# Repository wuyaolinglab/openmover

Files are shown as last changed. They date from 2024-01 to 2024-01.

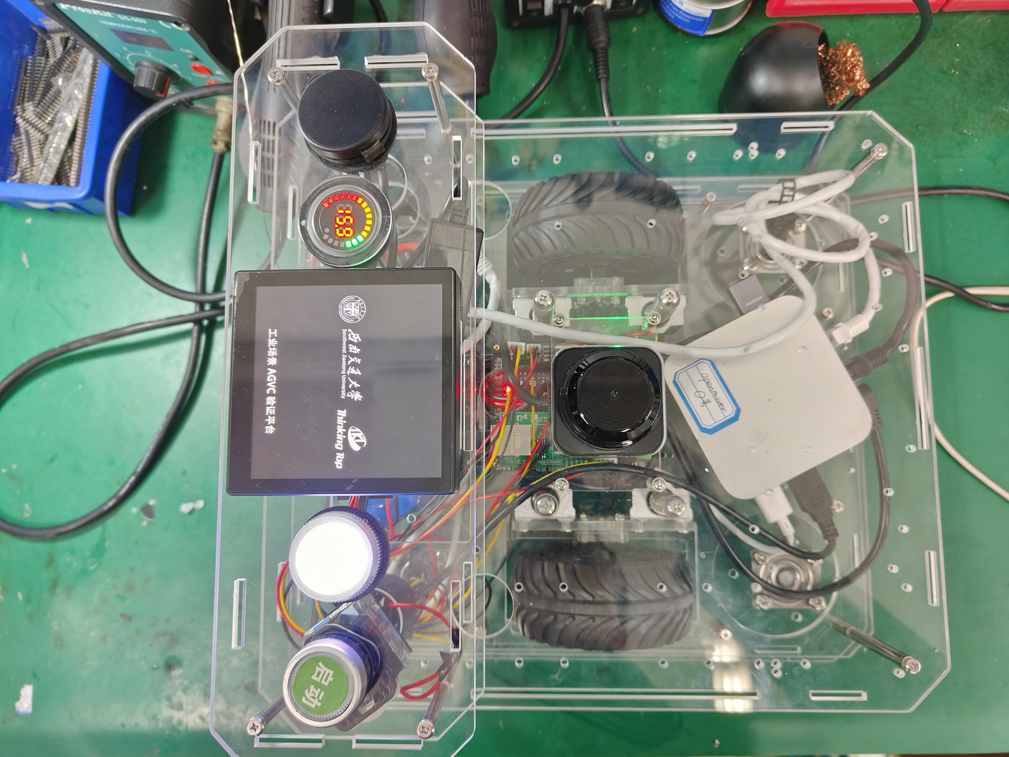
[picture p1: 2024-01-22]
相关图片/1.0原型机/顶部.jpg

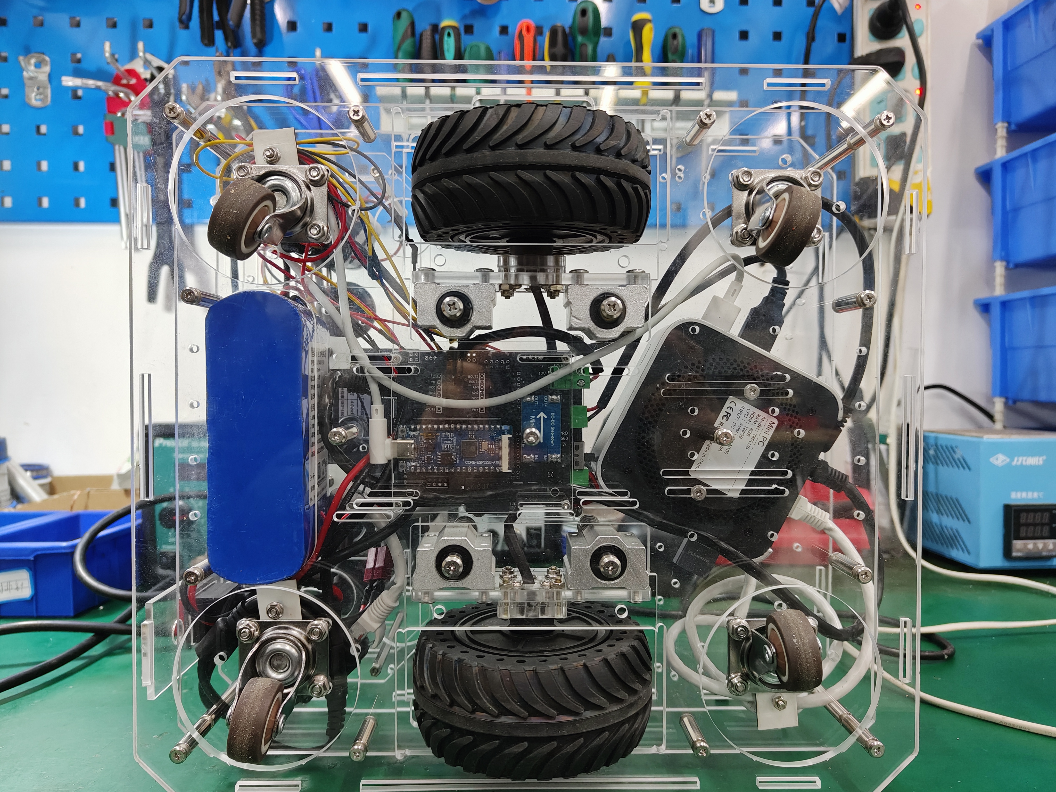
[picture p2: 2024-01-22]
相关图片/1.0原型机/底部.jpg

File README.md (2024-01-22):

# OPENMOVER

> 基于ROS的开源AGV机器人底盘

## 项目初衷

一切的源头来源于一个疑问：**有没有能陪伴我们从入门学习ROS到场景实际使用的机器人底盘开发项目？**

当我们打开淘宝浏览机器人底盘时，可以看到诸多基于树莓派和Jetson的小型ROS机器人底盘，也不乏体积庞大的工业级搬运底盘，前者往往只能陪伴我们度过最开始的学习开发，往往其结构与硬件绑定公司其他相关产品，因而我们在学习时的知识体系并不完善，需要我们之后单独学习底盘的结构设计以及电气控制部分；后者则往往不开放让我们进行学习开发的接口，结构上较为复杂且难以拆卸，往往其主控中的系统也并非基于ROS框架……

后来，带着上面的疑问我们开始围绕机器人底盘进行探索性的开发，我们一直在探索着如何保证低成本地简化工业底盘结构，如无必要勿增实体的思想指导着我们避免市面上的ROS机器人底盘为追求低成本和高销量而做出的无用设计，让结构尽可能简单；电气控制上尽可能简化到以模块为主，借鉴市面上的控制底盘没有冗余设计的教训，同时给容易坏、难设计的电源芯片、电机控制等部分预留更换可能，可能避免初学者因底盘的设计以及器件的偶尔损耗维修消磨兴趣……

再后来，我们在结合前面的诸多教训的基础上推出了OPENMOVER这个项目，希望能以这个项目来总结我们在前面探索机器人底盘设计中的经验与教训，将完整的机器人底盘设计思路提供给有意向探索机器人设计与应用的初学者，我们并非希望他们能避开机器人开发学习中的问题，只是更希望他们能在之后的开发设计中遇到问题时能对三个维度展开思考：我们的机器人要完成什么任务？为完成任务需要具备什么能力？为实现该能力，我的结构、硬件、软件设计有几种思路？

机器人的设计本质也是基于人的需要，设计一套复杂的系统并非我们的项目初衷，我们不愿意看到初学者迷失于技术之中，为自己贴上结构、硬件、软件开发的标签，而是去思考当我们作为用户去使用这套机器人时，我们希望得到什么？

当然啦，作为初版的设计者，我们希望这套机器人底盘足够简单可靠，能装上机械臂、举升平台、工程巡检设备等，能在不对结构进行较大改变的情况下拓展足够多的应用场景，从教学中应用到我们的实际业务场景中去，当然，我们的探索还在继续……

本项目遵循[Apache-2.0 license](https://github.com/wuyaolinglab/openmover#)协议

## 整体结构设计

更新时间24.1.22，版本1.0

### 1.0版本

设计导图文件可点击[这里查看](https://github.com/wuyaolinglab/openmover/tree/main/相关图片/1.0版结构与主控设计导图.png)

原型车图片可点击[这里查看](https://github.com/wuyaolinglab/openmover/tree/main/相关图片/1.0原型机)

1.0初版整车尺寸300x320xmm，整体结构采用双差速轮+四从动万向轮的结构，差速轮选用微雪DDSM115直驱伺服轮毂电机，四万向轮理论合计承重最高50KG

初版在外观结构上主要参考了海康威视AGV中的Q2系列LMR潜伏式机器人，并针对原有结构提出如下简化改进以及设计需要：

1. 主轮悬挂：主动轮添加悬挂结构，以保证整车在平地的路面适应能力以及运动性能
2. 雷达视野：初版使用蓝海LDS-50C-C30E单线TOF激光雷达，增大单线雷达的可视范围，减少结构上的遮挡角度范围
3. 较小尺寸：减小整车的尺寸，尽可能控制在320*320mm以内
4. 分层设计：保证整车的拓展能力，采用分层结构设计，底盘与可拓展部分为松耦合关系
5. 底盘布局：预留底盘内部拓展空间，方便理线与拓展元件
6. 电池限位：因供电需要至少4S电池组供电，尽可能在结构中加入单独的电池仓以防止电池固定不稳引发的安全问题
7. 负载能力：为保证整车的负载能力，底盘整体应尽可能考虑到受力均匀给到四个万向轮

我们提供了多种雷达的安装孔位，我们原型车使用到的是蓝海LDS-50C-C30E雷达，使用网口与工控机进行通讯，考虑到这款雷达可能不易在市场上购得，我们也测试过使用比较易得的镭神N10P系列雷达，大家可以根据手头的雷达安装孔位进行修改

## 底盘主控设计

更新时间24.1.20，版本1.1

### 1.1版本

初版底盘控制板采用合宙ESP32S3作为主控，工控机通过网口连接板载的有人双路UART转以太网模块USR-TCP232-E连接底盘主控以及串口屏，后续将上传以树莓派PICO作为主控，通过UART串口转USB模块与工控机进行通讯的方案

该版本的主要的考虑到的设计要点如下：

1. 尽可能减少贴片与插件元件的焊接，尽可能使用现有模块
2. 使用485总线转UART模块控制微雪伺服轮毂电机
3. 能控制双路有刷电池
4. 拥有外置灯效与按钮控制接口
5. 双路12V电源输出，支持的最大电流应保证在3A以上
6. 使用双路UART转以太网模块与工控机进行通讯，主控Type-C接口主要用于供电，后期将脱离使用
7. 底盘主控使用FreeRTOS系统，但为方便初学者烧录使用Arduino或PlatformIO作为开发平台

## 控制系统框架

更新时间24.1.20

底盘使用搭建了Ubuntu20.04.6操作系统的ROS [Noetic](http://wiki.ros.org/noetic/Installation/Ubuntu)作为机器人系统框架

相关例程适配代码将在后续更新中提供

## 物料清单及配件说明

本车物料均可于淘宝平台上购买、加工

主要元件为：

| 元件 | 型号 | 参考价格 |
| --- | --- | --- |
| TOF激光雷达 | [蓝海LDS-50C-C30E](https://detail.tmall.com/item.htm?id=670105361941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) | 2000 |
| TOF激光雷达 | [镭神N10P](https://item.taobao.com/item.htm?id=661905067052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) | 571.2 |
| 轮毂电机 | [微雪DDSM115直驱伺服电机](https://detail.tmall.com/item.htm?id=693013835916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) | 392 |
| N100工控机 | [T8PLUS/N100/DDR5](https://item.taobao.com/item.htm?id=690024926005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) | 740 |
| 14.8V锂电池组 | [亿森能14.8V10500毫安](https://item.taobao.com/item.htm?_u=l209b8sqkle3cb&id=723067674262&spm=a1z09.2.0.0.533a2e8dcV89pz) | 160 |
| 金属板材切割  | [5052铝板加工](https://item.taobao.com/item.htm?_u=l209b8sqkl377d&id=638490665708&spm=a1z09.2.0.0.418e2e8dOwLTBY) | 230~260  |

详细的物料清单将于下一更新中提供

## 上传说明

最近一次上传更新时间为24.1.20，整体版本1.0

项目文件与代码正在陆续上传更新中

***24.1.20*** 第一次上传，主要包括整车的结构设计、初版底盘控制板文件和简单物料清单

***24.1.22*** 第二次上传，修正了第一次上传中整车的结构设计细节，更新了说明资料包括图片、加工文件、模块说明文件，上传了相关配件的初版物料清单

## 更新计划

下一上传时间预计在24.1.25日前，预期更新版本为1.0

1. 增加整车的结构扩展说明，包括机械臂及举升平台的拓展设计安装方案
2. 更新整车的结构设计细节说明，同时准备上传ROS相关控制程序及初版说明
3. 增加对整体设计的说明
4. 更新参考资料及相关说明

## 收集意见

希望大家能在issues中提出你们对小车的改进与应用意见，我们将会及时回复并在整理后以月报进行发布

## 关于我们

本项目来自西南交通大学工训中心A510实验室团队

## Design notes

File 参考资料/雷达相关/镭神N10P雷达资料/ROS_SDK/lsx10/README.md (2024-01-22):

# lslidar

## Description

The `lslidar` package is a linux ROS driver for lslidar M10 ,L10,M10_GPS,M10_P,M10_PLUS and N10.
The package is tested on Ubuntu 20.04 with ROS indigo.

## Compling

This is a Catkin package. Make sure the package is on `ROS_PACKAGE_PATH` after cloning the package to your workspace. And the normal procedure for compling a catkin package will work.

```
cd your_work_space
catkin_make 
source devel/setup.bash
roslaunch lslidar_driver lslidar_net.launch 				(网口版雷达)
roslaunch lslidar_driver lslidar_serial.launch 				(串口版雷达)
```

open new terminal
rostopic pub -1 /lslidar_order std_msgs/Int8 "data: 1"		(open radar)
rostopic pub -1 /lslidar_order std_msgs/Int8 "data: 0"		(close radar)

```
open new terminal
source devel/setup.bash 
rostopic echo /difop_information					(printf information)
## Example Usage

### lslidar_m10_driver

**Parameters**

`device_ip` (`string`, `default: 192.168.1.222`)

By default, the IP address of the device is 192.168.1.222.

`frame_id` (`string`, `default: lslidar`)

The frame ID entry for the sent messages.

**Published Topics**

`lslidar_packets` (`lslidar_m10_msgs/LslidarM10Packet`)

Each message corresponds to a lslidar packet sent by the device through the Ethernet.

### lslidar_m10_decoder

**Parameters**

`min_range` (`double`, `0.3`)

`max_range` (`double`, `100.0`)

Points outside this range will be removed.

`frequency` (`frequency`, `20.0`)

Note that the driver does not change the frequency of the sensor. 

`publish_point_cloud` (`bool`, `false`)

If set to true, the decoder will additionally send out a local point cloud consisting of the points in each revolution.

**Published Topics**

`lslidar_sweep` (`lslidar_m10_msgs/LslidarM10Sweep`)

The message arranges the points within each sweep based on its scan index and azimuth.

`lslidar_point_cloud` (`sensor_msgs/PointCloud2`)

This is only published when the `publish_point_cloud` is set to `true` in the launch file.

**Node**

```

roslaunch lslidar_driver lslidar_net.launch

```

Note that this launch file launches both the driver and the decoder, which is the only launch file needed to be used.

## FAQ

## Bug Report

Prefer to open an issue. You can also send an E-mail to shaohuashu@lslidar.com

RERTION 
V0.1 2000 points per circle
v0.2 1000 points per circle

```

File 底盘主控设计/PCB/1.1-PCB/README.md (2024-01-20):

How to use：

At editor, open the document via: Top menu - File - Open - EasyEDA... , and select the json file, then open it at the editor, you can save it into a project.

如何使用：

打开编辑器，通过：顶部菜单 - 文件 - 打开 - 立创EDA... ，选择 json 文件打开在编辑器，你可以保存文档进工程里面。

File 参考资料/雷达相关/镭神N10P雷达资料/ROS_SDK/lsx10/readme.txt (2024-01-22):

版本变更
/***************************************************************
初始版本: LSLIDAR_M10_N10_V2.5.0_221103_ROS
变更内容: 
	1.实现M10/M10_P/M10_PLUS/N10/M10_GPS网口和串口传输数据生成点云功能
    	2.实现点云角度裁剪和距离过滤功能
    	3.可以通过lslidar_order话题控制雷达启
    	4.支持读取pcap包
	
更改日期: 2022-11-03
***************************************************************/

/***************************************************************
初始版本: LSLIDAR_M10_N10_V2.5.0_221103_ROS
变更版本: LSLIDAR_M10_N10_V2.5.1_221130_ROS
变更内容: 
	1.新增L10雷达。
	2.针对M10_P雷达出现的点云问题进行紧急修复。
	3.针对M10和M10_GPS雷达在最近出货雷达出现的点云问题进行紧急修复。
	4.修复循环索取新内存导致机器卡死bug。
	5.更新M10_P和M10_PLUS雷达协议。
	6.修复角度值分配错误问题。
	
更改日期: 2022-11-30
***************************************************************/
/***************************************************************
初始版本: LSLIDAR_M10_N10_V2.5.1_221130_ROS
变更版本: LSLIDAR_M10_N10_V2.5.2_230110_ROS
变更内容: 
	1.日常检测到驱动的包头检测有bug
	2.更新M10系列的角度补偿方法。
	3.修复发现的点角度不连续bug。
	4.添加可选择是否发布pointcloud2话题。
	5.添加可选择是否发布scan话题。
	6.添加双回波解析方法
	7.添加N10_P雷达选择1
	8.添加读txt文件功能
更改日期: 2023-01-10
***************************************************************/

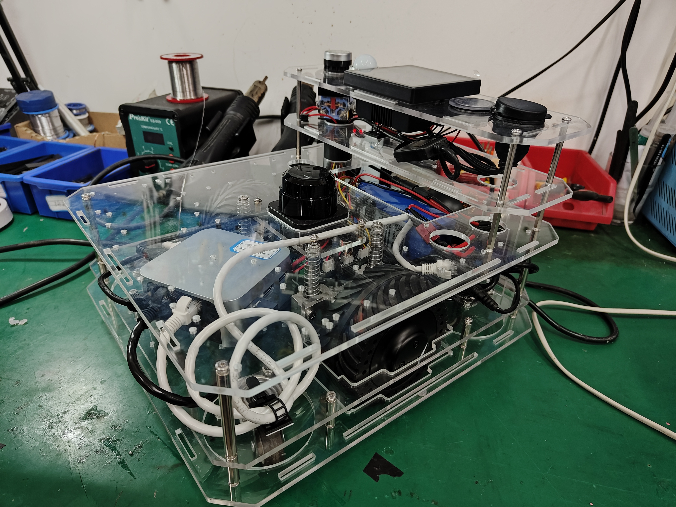
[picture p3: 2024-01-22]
相关图片/1.0原型机/前视图.jpg

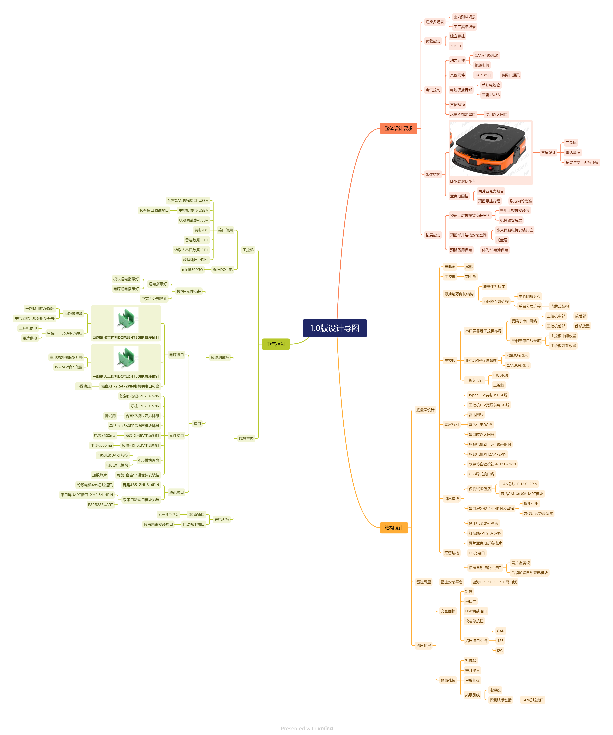
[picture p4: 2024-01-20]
相关图片/1.0版结构与主控设计导图.png

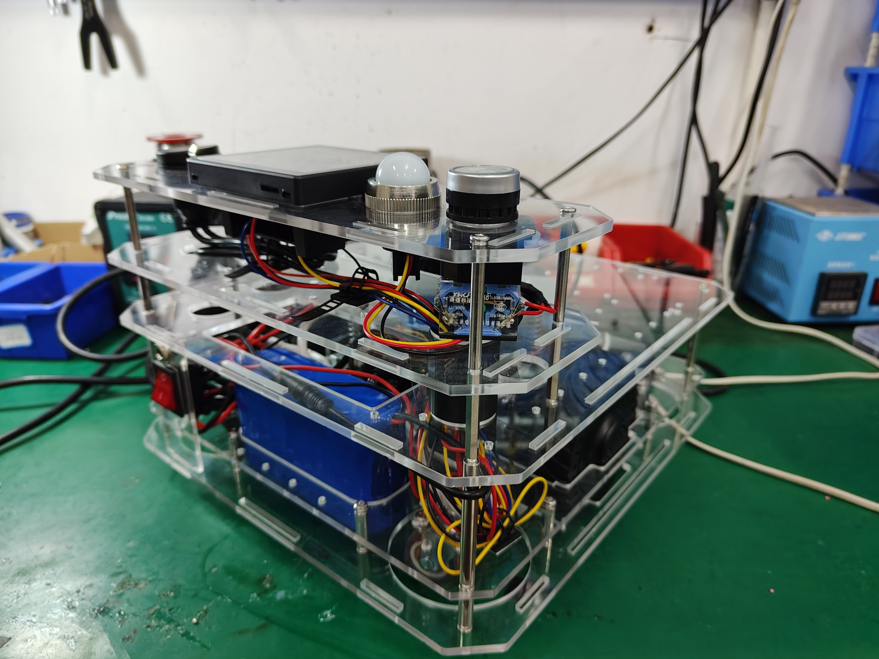
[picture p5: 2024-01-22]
相关图片/1.0原型机/后视图.jpg

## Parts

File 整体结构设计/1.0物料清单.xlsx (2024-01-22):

序号 | 所属模块 | 名称 | 规格型号 | 数量 | 单位 | 参考链接 | 备注
1 | 雷达 | 蓝海40m单线激光网口雷达 | LDS-50C-C30E | 1 | 个 | https://detail.tmall.com/item.htm?abbucket=15&id=670105361941&ns=1&skuId=4998133087692
2 | 雷达 | 镭神25m激光串口雷达 | N10P | 1 | 个 | https://item.taobao.com/item.htm?abbucket=17&id=661905067052&ns=1&skuId=5100312911950
3 | 电机 | 微雪直驱伺服电机 | DDSM115 | 2 | 台 | https://item.taobao.com/item.htm?_u=m209b8sqklf7e5&id=692477501151&skuId=5184823387964
4 | 工控机 | N100 mini主机电脑 | T8PLUS-8G内存-128GB存储 | 1 | 台 | https://item.taobao.com/item.htm?_u=l209b8sqkl6bb5&id=690024926005&sku_properties=5919063:25703169219
5 | 电池相关 | 14.8V锂电池组 | 10500mAh | 1 | 组 | https://item.taobao.com/item.htm?_u=l209b8sqkle3cb&id=723067674262&spm=a1z09.2.0.0.533a2e8dcV89pz
6 | 主控板模块 | 合宙ESP32S3开发板 | 8MPSRAM+16MFLASH | 1 | 个 | https://item.taobao.com/item.htm?_u=m209b8sqklf226&id=696836421009&spm=a1z09.2.0.0.238b2e8dYj4JwI
7 | 主控板模块 | 有人双串口转以太网模块 | USR-TCP232-E | 1 | 个 | https://detail.tmall.com/item.htm?_u=m209b8sqklc9fc&id=19968630199&spm=a1z09.2.0.0.238b2e8dYj4JwI
8 | 主控板模块 | KCUT485转UART模块 | TD321D485H-A | 1 | 个 | https://detail.tmall.com/item.htm?_u=m209b8sqkl5fd1&id=616272504011&spm=a1z09.2.0.0.238b2e8dYj4JwI
9 | 主控板模块 | DC-DC mini560降压稳压电源模块 | 12V输出 | 1 | 个 | https://item.taobao.com/item.htm?_u=m209b8sqkl0f66&id=633971374073&spm=a1z09.2.0.0.238b2e8dYj4JwI
10 | 外设 | 淘晶驰X2系列4英寸电容触摸串口屏 | 串口屏TJC4848X240_011C_Y | 1 | 个 | https://item.taobao.com/item.htm?_u=m209b8sqkl368c&id=688207991808&skuId=5076520715460
11 | 外设 | 宏科电防水圆形电压电量表双显表 | 16V四串锂电池显示 | 1 | 个 | https://item.taobao.com/item.htm?_u=m209b8sqklb6fb&id=623654981055&spm=a1z09.2.0.0.238b2e8dYj4JwI
12 | 外设 | LA38系列带符号按钮自锁复位 | LA38绿底启动升级款（银点） | 1 | 个 | https://item.taobao.com/item.htm?_u=m209b8sqkl3461&id=563811719494&sku_properties=1627207:28338
13 | 外设 | USB一公转二母数据延长线 | 1m | 1 | 根 | https://item.taobao.com/item.htm?_u=m209b8sqkl4fc1&id=639741255459&spm=a1z09.2.0.0.4b802e8dJ1Mi7y
14 | 外设 | KCD4船型开关 | 4脚2档红灯/铁脚 | 1 | 个 | https://item.taobao.com/item.htm?_u=m209b8sqkl44ed&id=546456098014&spm=a1z09.2.0.0.4b802e8dJ1Mi7y
15 | 外设 | DC-099 DC电源插座 | 5.5-2.1mm 全铜 | 1 | 个 | https://item.taobao.com/item.htm?_u=m209b8sqkld613&id=532739454749&spm=a1z09.2.0.0.4b802e8dJ1Mi7y
16 | 连接件 | 圆形M3金属柱 | M3*20+M3*40+M3*60单通 | 若干 |  | https://item.taobao.com/item.htm?_u=m209b8sqkl6134&id=711317105034&spm=a1z09.2.0.0.238b2e8dYj4JwI | 可视结构需要增减
17 | 连接件 | 不锈钢大平头倒边十字螺丝 | M3*12+M3*16+M4*14 | 若干 |  | https://detail.tmall.com/item.htm?_u=m209b8sqklc6d1&id=624099800280&spm=a1z09.2.0.0.4b802e8dJ1Mi7y
18 | 悬挂与支撑结构 | 万向轮 | 1.25寸TPE万向轮 | 4 | 个 | https://item.taobao.com/item.htm?_u=m209b8sqklcbe5&id=566448599482&spm=a1z09.2.0.0.238b2e8dYj4JwI
19 | 悬挂与支撑结构 | 直线滑块轴承 | SCS8UU | 4 | 个 | https://item.taobao.com/item.htm?_u=m209b8sqkl47ef&id=560816782190&sku_properties=122276018:20213
20 | 悬挂与支撑结构 | 镀铬棒光轴 | 8*80*两头M4牙 | 4 | 根 | https://item.taobao.com/item.htm?_u=m209b8sqklb9d4&id=727844415964&spm=a1z09.2.0.0.238b2e8dYj4JwI
21 | 悬挂与支撑结构 | 弹簧 | 1.2*13*50弹簧钢 | 4 | 个 | https://detail.tmall.com/item.htm?_u=m209b8sqkl4784&id=636771575448&spm=a1z09.2.0.0.4b802e8dJ1Mi7y
22 | 电池相关 | 16.8V锂电池充电器 | 16.8V3A 5.5*2.5mm | 1 | 个 | https://item.taobao.com/item.htm?_u=m209b8sqkl8316&id=581011361703&spm=a1z09.2.0.0.238b2e8dYj4JwI
23 | 线材相关 | 航模耐高温特软硅胶线 | 16AWG/1.5平方（5米） | 若干 |  | https://item.taobao.com/item.htm?_u=m209b8sqkl58fc&id=607953162190&spm=a1z09.2.0.0.238b2e8dYj4JwI
24 | 钣金加工 | 铝合金板加工定做 | 5052铝板加工定做加氧化和拉丝 | 3 | 片 | https://item.taobao.com/item.htm?_u=m209b8sqkl5ee2&id=638490665708&spm=a1z09.2.0.0.238b2e8dYj4JwI

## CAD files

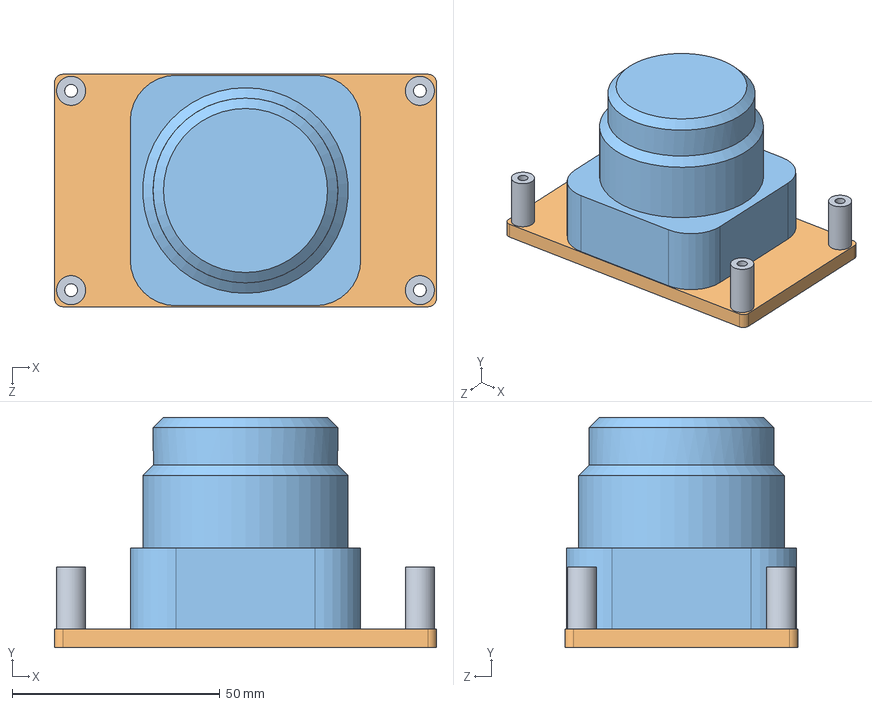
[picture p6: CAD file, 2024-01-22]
整体结构设计/openmover_chassis-1.0/1.0元器件模型/蓝海LDS-50C-C30E雷达安装平台.SLDASM
92.0 x 55.5 x 56.0 mm
15-M3-7MM隔离柱 x 4
全尺寸-蓝海LDS-50C-C30E-40m雷达潜藏平台
蓝海LDS-50C-C30E雷达模型

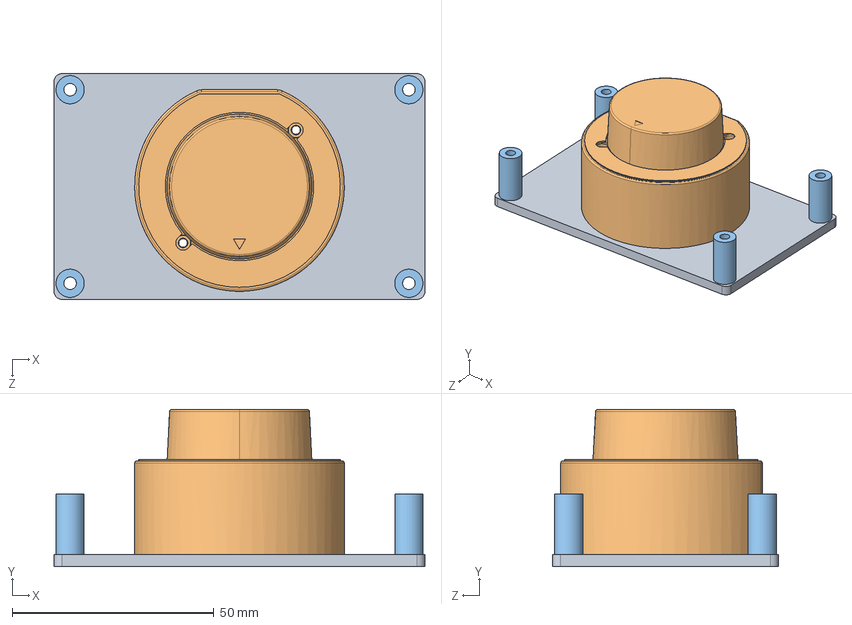
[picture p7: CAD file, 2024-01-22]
整体结构设计/openmover_chassis-1.0/1.0元器件模型/镭神雷达安装平台.SLDASM
92.0 x 39.0 x 56.0 mm
全尺寸-镭神N10P雷达潜藏平台
镭神N10P雷达模型
15-M3-7MM隔离柱 x 4

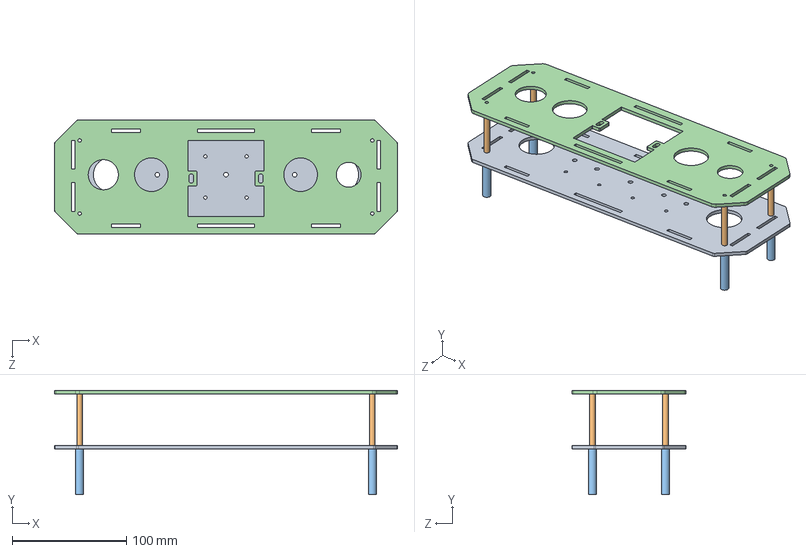
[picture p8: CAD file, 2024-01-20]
整体结构设计/openmover_chassis-1.0/1.0顶部扩展部分/承重顶部面板-可拓展举升.SLDASM
300.0 x 91.0 x 100.0 mm
顶层交互面板-平行尾部-下底
45-M3-5MM隔离柱 x 4
40-M3-7MM隔离柱 x 4
顶层交互面板-平行尾部-上盖

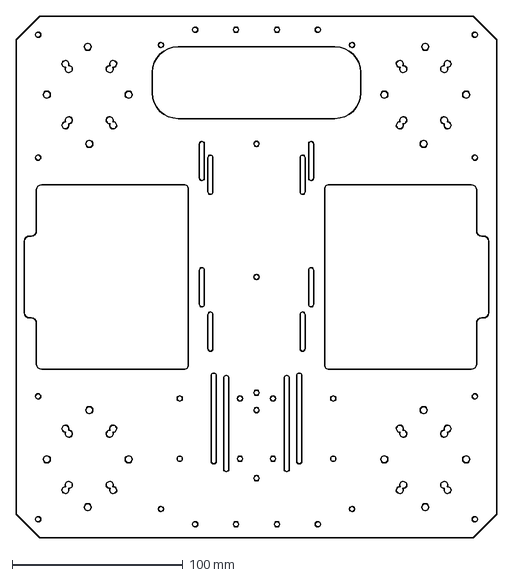
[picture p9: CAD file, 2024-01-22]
整体结构设计/openmover_chassis-1.0/1.0加工文件/Flat pattern - 万向轮层-连接隔层.DXF
281.8 x 305.8 mm

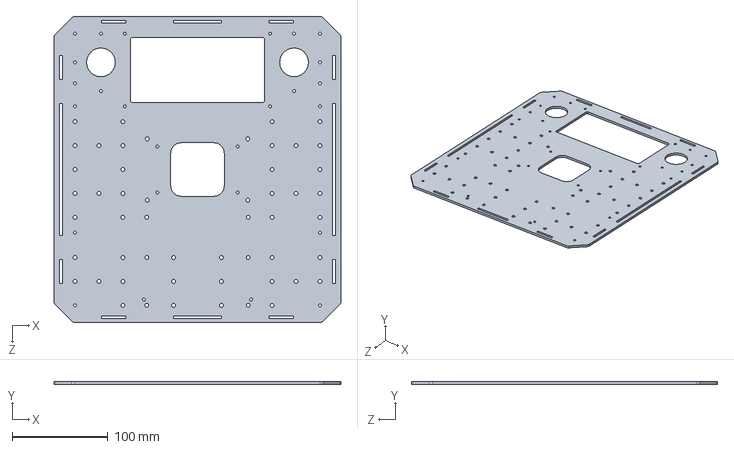
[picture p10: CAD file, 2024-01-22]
整体结构设计/openmover_chassis-1.0/1.0底盘部分/雷达层-悬挂上挂.SLDPRT
300.0 x 3.00 x 320.0 mm

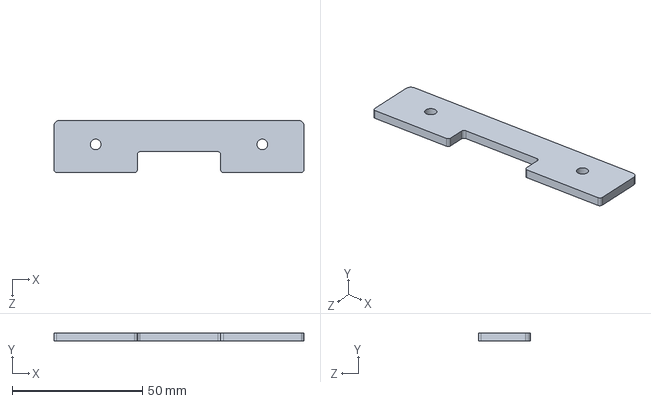
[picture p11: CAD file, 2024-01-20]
整体结构设计/openmover_chassis-1.0/1.0悬挂设计/悬挂下部加高垫.SLDPRT
96.0 x 3.00 x 20.0 mm

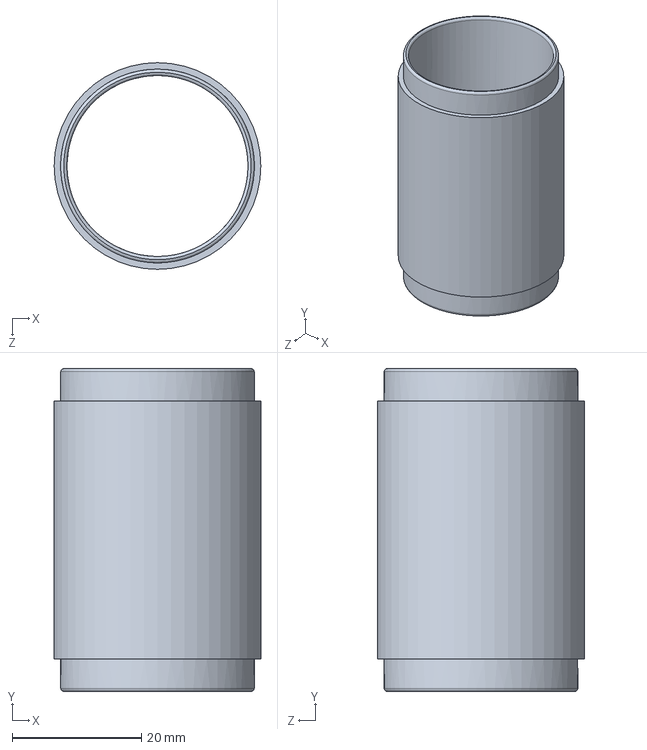
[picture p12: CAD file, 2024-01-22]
整体结构设计/openmover_chassis-1.0/1.0连接件/40-28MM-32MM走线隔离柱.SLDPRT
32.0 x 50.0 x 32.0 mm

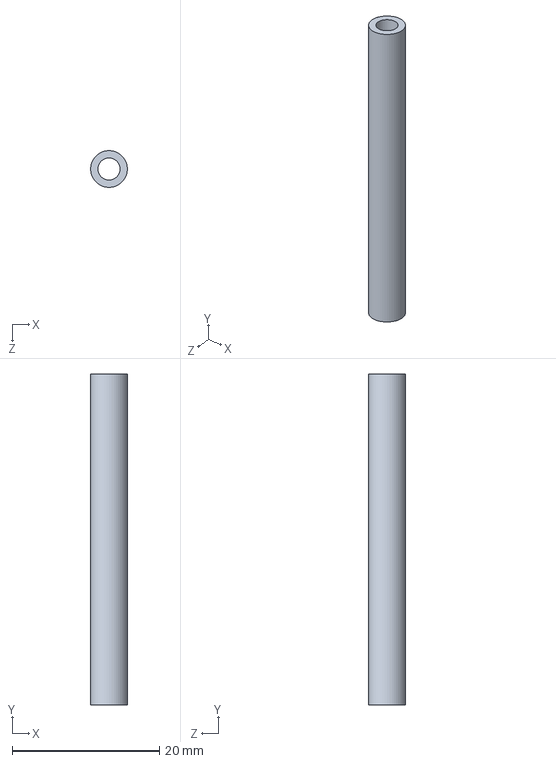
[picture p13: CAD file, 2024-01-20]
整体结构设计/openmover_chassis-1.0/1.0顶部扩展部分/45-M3-5MM隔离柱.SLDPRT
5.00 x 45.0 x 5.00 mm

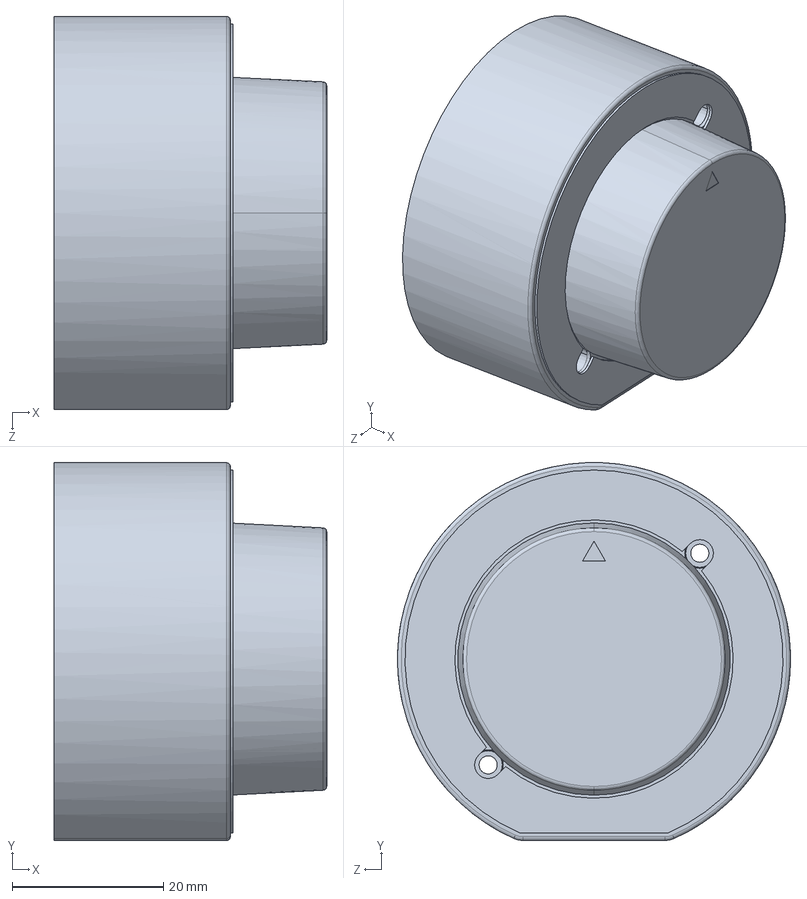
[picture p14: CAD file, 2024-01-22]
整体结构设计/openmover_chassis-1.0/1.0元器件模型/镭神N10P雷达模型.SLDPRT
36.0 x 50.0 x 52.0 mm

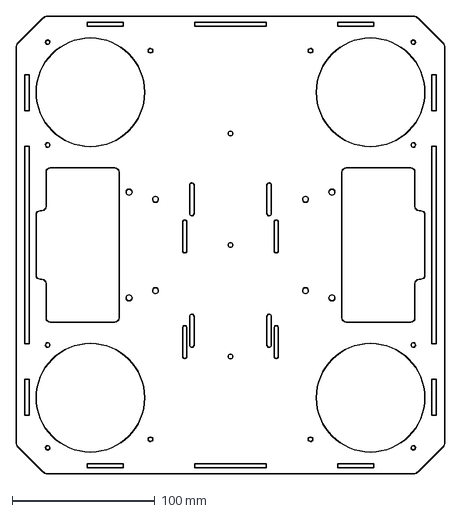
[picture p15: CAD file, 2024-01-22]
整体结构设计/openmover_chassis-1.0/1.0加工文件/Flat pattern - 底盘层-悬挂安装层.DXF
300.0 x 320.0 mm

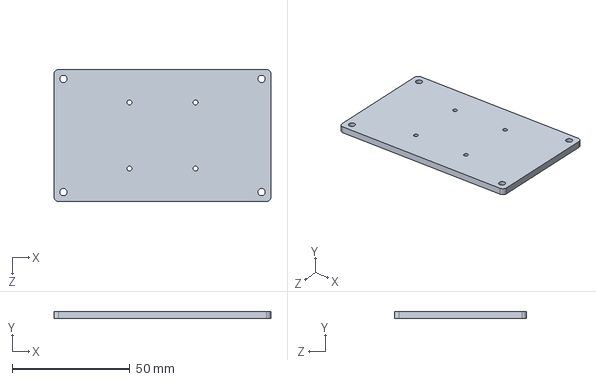
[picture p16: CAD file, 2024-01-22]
整体结构设计/openmover_chassis-1.0/1.0底盘部分/全尺寸-镭神N10P雷达潜藏平台.SLDPRT
92.0 x 3.00 x 56.0 mm

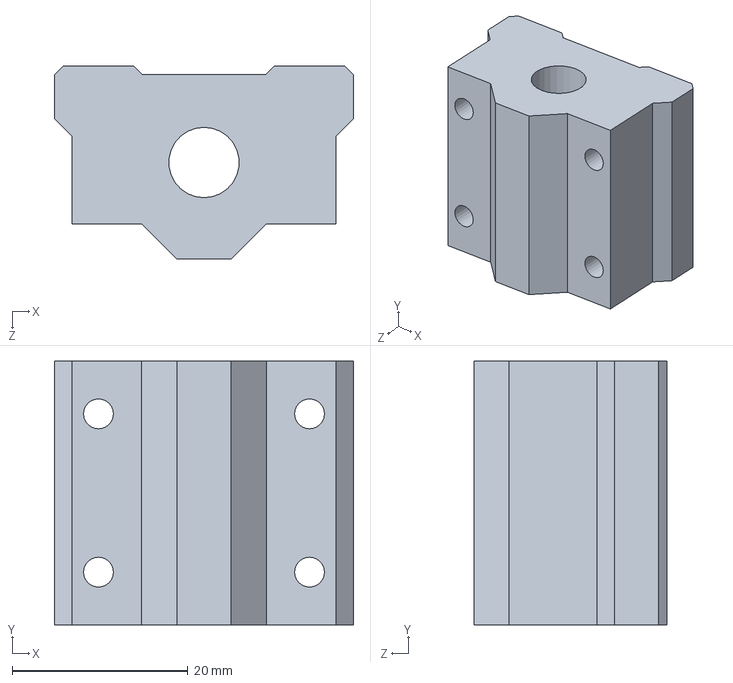
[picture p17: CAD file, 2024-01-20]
整体结构设计/openmover_chassis-1.0/1.0悬挂设计/SCS8-M4+3.4固定孔直线滑块.SLDPRT
34.0 x 30.0 x 22.0 mm

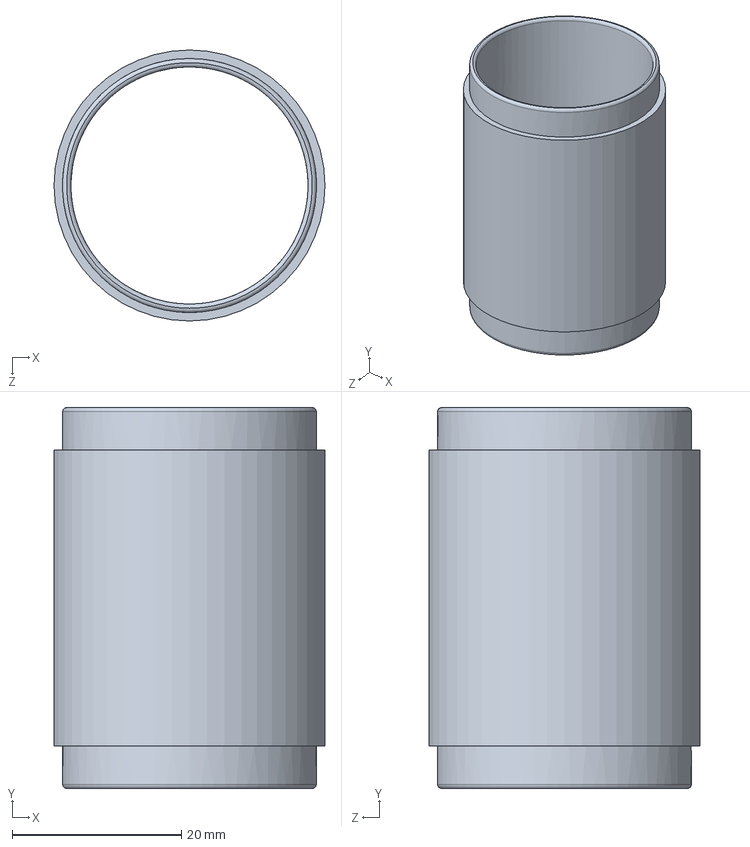
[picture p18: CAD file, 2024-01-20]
整体结构设计/openmover_chassis-1.0/1.0连接件/35-28MM-32MM走线隔离柱.SLDPRT
32.0 x 45.0 x 32.0 mm

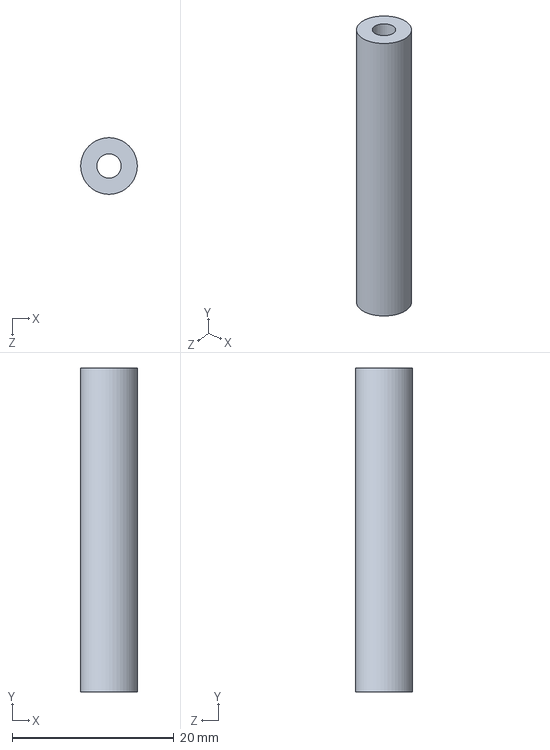
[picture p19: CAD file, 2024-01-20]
整体结构设计/openmover_chassis-1.0/1.0顶部扩展部分/40-M3-7MM隔离柱.SLDPRT
7.00 x 40.0 x 7.00 mm

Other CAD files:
整体结构设计/openmover_chassis-1.0/1.0加工文件/Flat pattern - 雷达层-悬挂上挂.DXF
整体结构设计/openmover_chassis-1.0/1.0底盘部分/底盘亚克力围挡.SLDPRT
整体结构设计/openmover_chassis-1.0/1.0悬挂设计/80-8MM光轴.SLDPRT
整体结构设计/openmover_chassis-1.0/1.0连接件/60-M3-7MM隔离柱.SLDPRT
整体结构设计/openmover_chassis-1.0/1.0元器件模型/N100工控机模型.SLDPRT
整体结构设计/openmover_chassis-1.0/1.0元器件模型/四串三并电池模型.SLDPRT
整体结构设计/openmover_chassis-1.0/1.0元器件模型/蓝海LDS-50C-C30E雷达模型.SLDPRT
整体结构设计/openmover_chassis-1.0/1.0底盘部分/万向轮层-连接隔层.SLDPRT
整体结构设计/openmover_chassis-1.0/1.0底盘部分/全尺寸-蓝海LDS-50C-C30E-40m雷达潜藏平台.SLDPRT
整体结构设计/openmover_chassis-1.0/1.0底盘部分/底盘亚克力后部围挡.SLDPRT
整体结构设计/openmover_chassis-1.0/1.0底盘部分/底盘层-悬挂安装层.SLDPRT
整体结构设计/openmover_chassis-1.0/1.0底盘部分/电池仓盖板.SLDPRT
整体结构设计/openmover_chassis-1.0/1.0悬挂设计/SCS8-轮毂电机.SLDPRT
整体结构设计/openmover_chassis-1.0/1.0悬挂设计/走线垫片-轮毂电机.SLDPRT
整体结构设计/openmover_chassis-1.0/1.0连接件/15-M3-7MM隔离柱.SLDPRT
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

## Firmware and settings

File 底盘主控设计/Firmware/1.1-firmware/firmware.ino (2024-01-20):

#include <Arduino.h>
#include "led.h"
#include "button.h"
#include "motor.h"
#include "config.h"
#include "esp_task_wdt.h"

// 通讯相关变量
String comm_recv_buffer = "";
String comm_send_buffer = "";
uint8_t comm_state = COMM_STATE_WAITFORHEAD;

// 外设相关变量
motor_cmd comm_motor_cmd_data;
motor_response comm_motor_response_data;
uint8_t comm_button_data = 0;
uint8_t comm_led_color_data = 0;

void comm_send_handler(void *pt)
{
	while (1)
	{
		// 获取实时数据
		xQueueReceive(motor_response_queue, &comm_motor_response_data, 0);
		xQueueReceive(button_queue, &comm_button_data, 0);

		// 发送数据
		comm_send_buffer = COMM_HEAD;
		comm_send_buffer += comm_motor_response_data.speed_left_rpm;
		comm_send_buffer += COMM_FILTER;
		comm_send_buffer += comm_motor_response_data.speed_right_rpm;
		comm_send_buffer += COMM_FILTER;
		comm_send_buffer += comm_motor_response_data.counter_left_pulses;
		comm_send_buffer += COMM_FILTER;
		comm_send_buffer += comm_motor_response_data.counter_right_pulses;
		comm_send_buffer += COMM_FILTER;
		comm_send_buffer += comm_motor_response_data.error_code_left;
		comm_send_buffer += COMM_FILTER;
		comm_send_buffer += comm_motor_response_data.error_code_right;
		comm_send_buffer += COMM_FILTER;
		comm_send_buffer += comm_button_data;
		comm_send_buffer += COMM_TAIL;
		COMM_SERIAL.println(comm_send_buffer);

		// 100Hz 运行
		vTaskDelay(COMM_CONTROL_PERIOD / portTICK_PERIOD_MS);
	}

	vTaskDelete(NULL);
}

void comm_recv_handler(void *pt)
{
	while (1)
	{
		// 接收数据
		while (COMM_SERIAL.available())
		{
			char current_char = COMM_SERIAL.read();

			if (current_char == COMM_HEAD)
			{
				comm_recv_buffer = "";
				comm_state = COMM_STATE_WAITFORTAIL;
			}
			else if (comm_state == COMM_STATE_WAITFORTAIL && current_char == COMM_TAIL)
			{
				int data_index = 0;
				int last_filter_pos = 0;
				int buffer_length = comm_recv_buffer.length();

				for (int i = 0; i < buffer_length; i++)
				{
					if (comm_recv_buffer.charAt(i) == COMM_FILTER || i == buffer_length - 1)
					{
						if (data_index == 0)
						{
							comm_motor_cmd_data.cmd_left_rpm = comm_recv_buffer.substring(last_filter_pos, i).toInt();
						}
						else if (data_index == 1)
						{
							comm_motor_cmd_data.cmd_right_rpm = comm_recv_buffer.substring(last_filter_pos + 1, i).toInt();
						}
						else if (data_index == 2)
						{
							comm_led_color_data = comm_recv_buffer.substring(last_filter_pos + 1, buffer_length).toInt();
						}

						last_filter_pos = i;
						data_index++;
					}
				}

				comm_recv_buffer = "";
				comm_state = COMM_STATE_WAITFORHEAD;
			}
			else if (comm_state == COMM_STATE_WAITFORTAIL)
			{
				comm_recv_buffer += current_char;

				if (comm_recv_buffer.length() >= COMM_MAX_BUFFER_SIZE)
				{
					comm_recv_buffer = "";
					comm_state = COMM_STATE_WAITFORHEAD;
				}
			}
		}

		// 指令发送到队列
		xQueueOverwrite(motor_cmd_queue, &comm_motor_cmd_data);
		xQueueOverwrite(led_queue, &comm_led_color_data);

		// 100Hz 运行
		vTaskDelay(COMM_CONTROL_PERIOD / portTICK_PERIOD_MS);
	}

	vTaskDelete(NULL);
}

void setup()
{
	// 初始化串口
	COMM_SERIAL.begin(COMM_BAUDRATE, SERIAL_8N1, 2, 1);

	// 初始化外设任务
	led_init();
	button_init();
	motor_init();

	// 初始化通讯任务
	// 创建发送任务，绑定到核心1
	xTaskCreatePinnedToCore(
		comm_send_handler,
		"comm_send_handler",
		4096,
		NULL,
		1,
		NULL,
		1);

	// 创建接收任务，绑定到核心1
	xTaskCreatePinnedToCore(
		comm_recv_handler,
		"comm_recv_handler",
		4096,
		NULL,
		1,
		NULL,
		1);

	// 启动看门狗
	esp_task_wdt_init(WDT_TIMEOUT, true);
	esp_task_wdt_add(NULL);
}

void loop()
{
	// 喂狗
	esp_task_wdt_reset();

	// 延时
	vTaskDelay(WDT_FEED_PERIOD / portTICK_PERIOD_MS);
}

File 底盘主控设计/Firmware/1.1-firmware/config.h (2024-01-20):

#ifndef CONFIG_H
#define CONFIG_H

#define configMINIMAL_STACK_SIZE 245756

// 看门狗部分设置
#define WDT_TIMEOUT 1
#define WDT_FEED_PERIOD 100

// 按钮部分设置
#define BUTTON_CONTROL_PERIOD 20
#define BUTTON_PIN 8

// LED部分设置
#define LED_CONTROL_PERIOD 50
#define LED_DATA_PIN 9
#define LED_TYPE WS2811
#define LED_NUM 50
#define LED_COLOR_ORDER GRB

// 电机部分设置
#define MOTOR_CONTROL_PERIOD 5
#define MOTOR_SERIAL Serial2
#define MOTOR_BAUDRATE 115200l
#define MOTOR_LEFT_ID 1
#define MOTOR_RIGHT_ID 2
#define MOTOR_MAX_RPM 330
#define MOTOR_CMD_BUFFER_SIZE 10
#define MOTOR_RECV_BUFFER_SIZE 10
#define MOTOR_RECV_TIMEOUT 100
#define MOTOR_PULSE_PER_ROUND 4096

// 主从通讯设置
#define COMM_SERIAL Serial1
#define COMM_CONTROL_PERIOD 10
#define COMM_BAUDRATE 230400l
#define COMM_HEAD '#'
#define COMM_TAIL '!'
#define COMM_FILTER ' '
#define COMM_STATE_WAITFORHEAD 0
#define COMM_STATE_WAITFORTAIL 1
#define COMM_MAX_BUFFER_SIZE 256

#endif

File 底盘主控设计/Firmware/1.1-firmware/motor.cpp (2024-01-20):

#include "motor.h"

// 电机控制量队列
QueueHandle_t motor_cmd_queue;
// 电机反馈量队列
QueueHandle_t motor_response_queue;

// 电机控制量
motor_cmd motor_cmd_data;

// 电机反馈量
motor_response motor_response_data;

// 电机控制量buffer
uint8_t motor_cmd_buffer[MOTOR_CMD_BUFFER_SIZE] = {0x00};
uint8_t motor_recv_buffer[MOTOR_RECV_BUFFER_SIZE] = {0x00};

// 上一次收到数据的时候与这一次收到数据的时间
unsigned long last_recv_time_left_ms = 0;
unsigned long last_recv_time_right_ms = 0;
unsigned long recv_time_left_ms = 0;
unsigned long recv_time_right_ms = 0;

void motor_init()
{
    // 初始化队列
    motor_cmd_queue = xQueueCreate(1, sizeof(motor_cmd));
    motor_response_queue = xQueueCreate(10, sizeof(motor_response));

    // 初始化串口
    MOTOR_SERIAL.begin(MOTOR_BAUDRATE, SERIAL_8N1, 7, 6);

    // 创建任务，绑定到核心0
    xTaskCreatePinnedToCore(
        motor_handler,
        "motor_handler",
        8192,
        NULL,
        3,
        NULL,
        0);
}

void motor_build_cmd_frame(uint8_t *buffer, uint8_t motor_id, int16_t speed_rpm)
{
    // 防止速度出错
    speed_rpm = abs(speed_rpm) > MOTOR_MAX_RPM ? copysign(MOTOR_MAX_RPM, speed_rpm) : speed_rpm;

    // 数据帧
    buffer[0] = motor_id;
    buffer[1] = 0x64;
    buffer[2] = (uint8_t)(speed_rpm >> 8);
    buffer[3] = (uint8_t)(speed_rpm & 0xFF);
    buffer[4] = 0x00;
    buffer[5] = 0x00;
    buffer[6] = 0x00;
    buffer[7] = 0x00;
    buffer[8] = 0x00;

    // CRC校验
    buffer[MOTOR_RECV_BUFFER_SIZE - 1] = crc8_maxim(buffer, MOTOR_RECV_BUFFER_SIZE - 1);
}

void motor_parse_response_frame(uint8_t *buffer, uint8_t motor_id, motor_response &data)
{
    if (motor_id == buffer[0] &&
        crc8_maxim(buffer, MOTOR_RECV_BUFFER_SIZE - 1) == buffer[MOTOR_RECV_BUFFER_SIZE - 1])
    {
        // 计算速度
        int16_t speed = ((int16_t)buffer[4] << 8) | buffer[5];

        if (motor_id == MOTOR_LEFT_ID)
        {
            recv_time_left_ms = millis();

            if (last_recv_time_left_ms != 0)
            {
                data.speed_left_rpm = speed;
                data.counter_left_pulses += (int64_t)(((float)speed) *
                                                      ((float)(recv_time_left_ms - last_recv_time_left_ms)) * ((float)MOTOR_PULSE_PER_ROUND) / 60000.0f);
                data.error_code_left = buffer[8];
            }

            last_recv_time_left_ms = recv_time_left_ms;
        }
        else if (motor_id == MOTOR_RIGHT_ID)
        {
            recv_time_right_ms = millis();

            if (last_recv_time_right_ms != 0)
            {
                data.speed_right_rpm = speed;
                data.counter_right_pulses += (int64_t)(((float)speed) *
                                                       ((float)(recv_time_right_ms - last_recv_time_right_ms)) * ((float)MOTOR_PULSE_PER_ROUND) / 60000.0f);
                data.error_code_right = buffer[8];
            }

            last_recv_time_right_ms = recv_time_right_ms;
        }
    }
}

void motor_handler(void *pt)
{
    while (1)
    {
        // 等待电机指令
        if (xQueueReceive(motor_cmd_queue, &motor_cmd_data, 0))
        {
            // 发送指令到左电机
            motor_build_cmd_frame(motor_cmd_buffer, MOTOR_LEFT_ID, motor_cmd_data.cmd_left_rpm);
            MOTOR_SERIAL.setTimeout(MOTOR_RECV_TIMEOUT);
            MOTOR_SERIAL.write(motor_cmd_buffer, MOTOR_CMD_BUFFER_SIZE);

            // 等待并解析左电机反馈
            if (MOTOR_SERIAL.readBytes(motor_recv_buffer, MOTOR_RECV_BUFFER_SIZE) ==
                MOTOR_RECV_BUFFER_SIZE)
            {
                motor_parse_response_frame(motor_recv_buffer, MOTOR_LEFT_ID, motor_response_data);
            }

            // 发送指令到右电机
            motor_build_cmd_frame(motor_cmd_buffer, MOTOR_RIGHT_ID, motor_cmd_data.cmd_right_rpm);
            MOTOR_SERIAL.setTimeout(MOTOR_RECV_TIMEOUT);
            MOTOR_SERIAL.write(motor_cmd_buffer, MOTOR_CMD_BUFFER_SIZE);

            // 等待并解析右电机反馈
            if (MOTOR_SERIAL.readBytes(motor_recv_buffer, MOTOR_RECV_BUFFER_SIZE) ==
                MOTOR_RECV_BUFFER_SIZE)
            {
                motor_parse_response_frame(motor_recv_buffer, MOTOR_RIGHT_ID, motor_response_data);
            }

            // 发送反馈数据到队列
            xQueueSend(motor_response_queue, &motor_response_data, 0);
        }

        // 200Hz 运行
        vTaskDelay(MOTOR_CONTROL_PERIOD / portTICK_PERIOD_MS);
    }

    vTaskDelete(NULL);
}

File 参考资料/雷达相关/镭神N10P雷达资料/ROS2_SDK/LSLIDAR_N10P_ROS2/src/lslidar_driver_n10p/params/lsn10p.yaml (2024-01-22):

/lslidar_driver_node:
  ros__parameters: 
    frame_id: laser                                       #激光坐标
    group_ip: 224.1.1.2
    add_multicast: false 
    device_ip: 192.168.1.200                   	            #雷达源IP
    device_ip_difop: 192.168.1.102                          #雷达目的ip
    msop_port: 2368                                         #雷达目的端口号
    difop_port: 2369                                        #雷达源端口号
    lidar_name: N10_P                                         #雷达选择:M10 M10_P M10_PLUS M10_GPS N10 L10 N10_P
    angle_disable_min: 130.0                                  #角度裁剪开始值
    angle_disable_max: 225.0                                  #角度裁剪结束值
    min_range: 0.0                                          #雷达接收距离最小值
    max_range: 200.0                                        #雷达接收距离最大值
    use_gps_ts: false                                       #雷达是否使用GPS授时
    scan_topic: /scan                                       #设置激光数据topic名称
    interface_selection: serial                             #接口选择:net 为网口,serial 为串口。
    serial_port_: /dev/wheeltec_laser                              #串口连接时的串口号
    high_reflection: false                                  #M10_P雷达需填写该值,若不确定，请联系技术支持。
    compensation: false				                              #M10系列是否使用角度补偿功能
    pubScan: true                                           #是否发布scan话题
    pubPointCloud2: false                                    #是否发布pointcloud2话题
    pointcloud_topic: /lslidar_point_cloud                  #设置激光数据topic名称
#    pcap: /home/ls/1.pcap                                  #雷达是否使用pcap包读取功能
#    in_file_name: /home/ls/1.txt                           #雷达是否使用txt文件读取功能

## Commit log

2024-01-20 第一次上传更新
    [15-M3-7MM隔离柱.SLDPRT, 20-M2-3.2MM隔离柱.SLDPRT, 20-M3-7MM隔离柱.SLDPRT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]
2024-01-22 修正了第一次上传中整车的结构设计细节，更新了说明资料包括图片、加工文件、模块说明文件，上传了相关配件的初版物料清单
    [1.0物料清单.xlsx, 40-28MM-32MM走线隔离柱.SLDPRT, Flat pattern - 万向轮层-连接隔层.DXF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]
